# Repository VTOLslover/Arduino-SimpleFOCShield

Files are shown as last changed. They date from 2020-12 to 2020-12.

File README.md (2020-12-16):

# Arduino *Simple**FOC**Shield* *v2.0* - *(testing)*

This is an open-source low-cost Brushless DC (BLDC) motor driver board intended primarily for low-power FOC applications up to 5Amps. The board is fully compatible with the Arduino UNO and all the boards with the standard Arduino headers. The *Simple**FOC**Shield*, in combination with the *Simple**FOC**library* provides user-friendly way to control BLDC motors both in hardware and software.

<p align="">
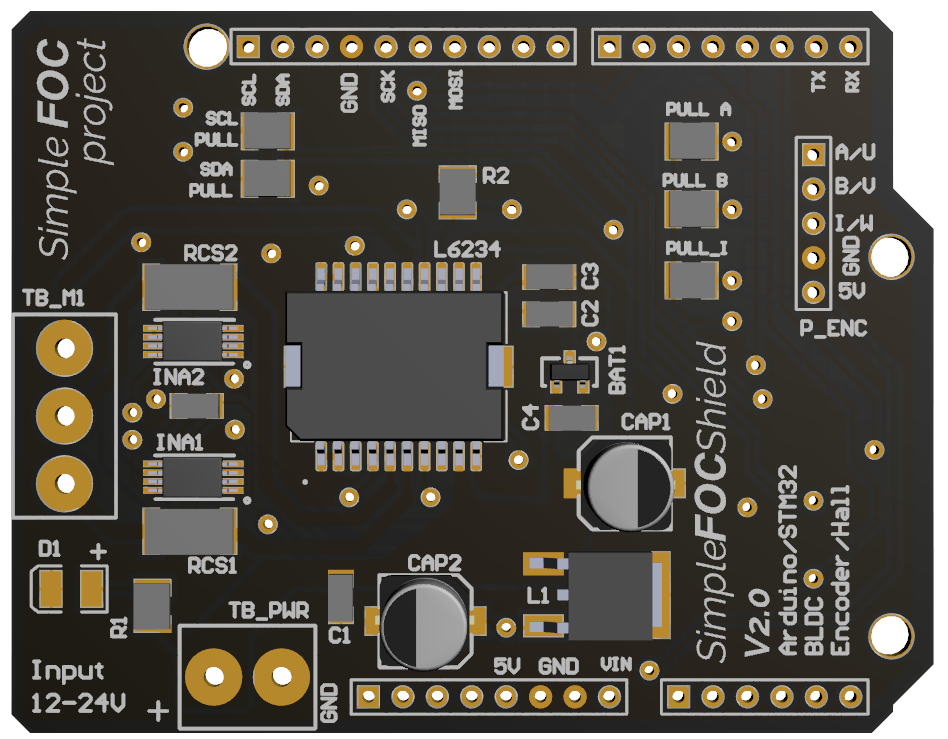
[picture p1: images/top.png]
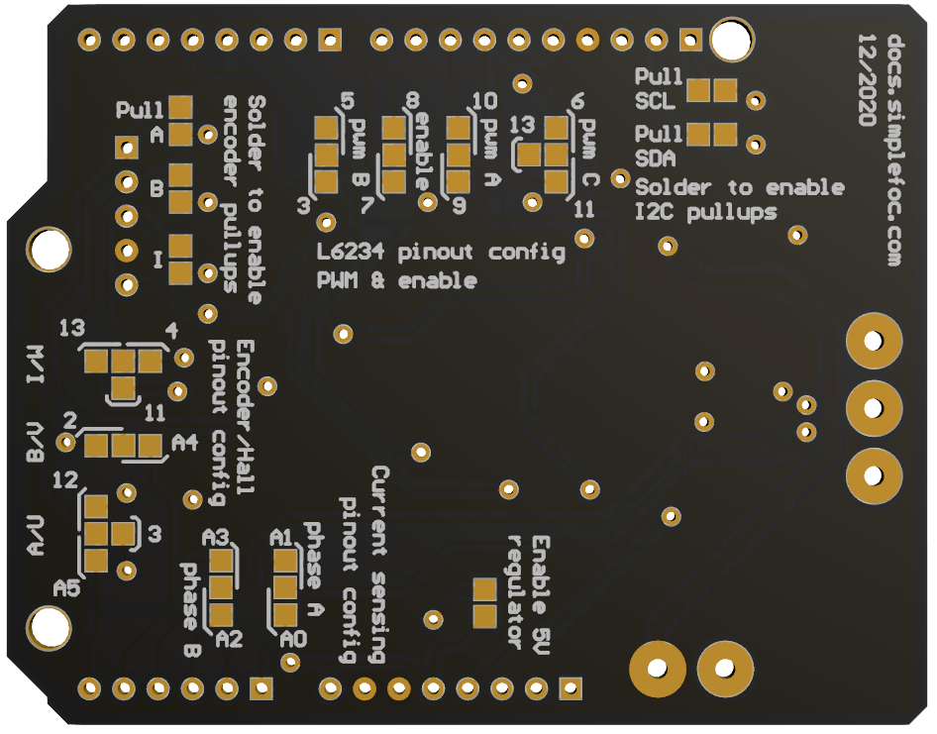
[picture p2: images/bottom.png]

</p>

### Features
- **Plug & play**: In combination with Arduino *Simple**FOC**library* - [github](https://github.com/simplefoc/Arduino-FOC)
- **Low-cost**: Price of €15 - [Check the pricing](https://www.simplefoc.com/simplefoc_shield_product) 
- **Max power 120W** - max current 5A, power-supply 12-24V
   - Designed for Gimbal motors with the internal resistance >10 Ωs. 
- **Stackable**: running 2 motors in the same time
- **Encoder/Hall sensors interface**: Integrated 3.3kΩ pullups (configurable)
- **I2C interface**: Integrated 4.7kΩ pullups (configurable)
- **Configurable pinout**: Hardware configuration - soldering connections
- **Arduino headers**: Arduino UNO, Arduino MEGA, STM32 Nucleo boards...
- **Open Source**: Fully available fabrication files - [how to make it yourself](https://docs.simplefoc.com/arduino_simplefoc_shield_fabrication)

### New Features 
- **In-line Current sensing** 
   - Up to 3Amps bi-directional
   - Real FOC torque control
- 5V voltage regulator
   - configurable - enable/disable
- New pinout for hardware config
- Still optimised for ordering from JLCPCB

### Short YouTube demonstration video :D
<p align="">
<a href="https://youtu.be/G5pbo0C6ujE">

</a>
</p>

## Board versions:

To check the release timeline, click [here](https://github.com/simplefoc/Arduino-SimpleFOCShield/releases) 

Version  |link | Release date | Comment
----- | ----- | ---- | ----
*Simple**FOC**Shield* v1.3 |[release v1.3](https://github.com/simplefoc/Arduino-SimpleFOCShield/releases/tag/v1.3) | 04/20 | Inital release
*Simple**FOC**Shield* v1.3.1 | [release v1.3.1](https://github.com/simplefoc/Arduino-SimpleFOCShield/releases/tag/v1.3.1) | 07/20 | added Nucleo stacking support
*Simple**FOC**Shield* v1.3.2 |[release v1.3.2](https://github.com/simplefoc/Arduino-SimpleFOCShield/releases/tag/v1.3.2) | 09/20 | added I2C pullups
*Simple**FOC**Shield* v1.3.3 |[release v1.3.3](https://github.com/simplefoc/Arduino-SimpleFOCShield/releases/tag/v1.3.3) | 12/20 | addapted L6234 circuit + full Arduino header

## Getting started
You already have your own <span class="simple">Simple<span class="foc">FOC</span>Shield</span>? <br>
[Here is a simple guide how to start preparing your setup](https://docs.simplefoc.com/arduino_simplefoc_shield_getting_started)

## How to get hold of the <span class="simple">Simple<span class="foc">FOC</span>Shield</span> 
- **Fabricate the board yourself**:  Please visit the [board fabrication](https://docs.simplefoc.com/arduino_simplefoc_shield_fabrication) to find out how to manufacture the board yourself!<br>
- **Order the finished and tested board**:  Check out our [shop](https://simplefoc.com/simplefoc_shield_product).

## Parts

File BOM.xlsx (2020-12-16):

Designator | Comment | Manufacturer Part Number or Seeed SKU | Qty | Link
C1 | 1206 100nF | C1206C104M5RECAUTO | 1 | https://www.mouser.com/
C2 | 1206 10nF | C1206C103J3RAUTO | 1 | 'https://www.mouser.com/
C3 | 1206 1uF | C1206X105K3RAC3316 | 1 | 'https://www.mouser.com/
C4 | 1206 220nF | C1206C224J5RECAUTO7210 | 1 | 'https://www.mouser.com/
CAP2 | 10uF | VZH100M1HTR-0606 (https://octopart-clicks.com/click/altium?sku=667-EEH-ZA1E101XP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) | 1 | 'https://www.mouser.com/
CAP1 | 100uF | EEEHAV101XAP (https://octopart-clicks.com/click/altium?sku=667-EEH-ZA1E101XP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) | 1 | 'https://www.mouser.com/
BAT1 | BAT54S | TBAT54S,LM (https://octopart-clicks.com/click/altium?manufacturer=ON%20Semiconductor%20%2F%20Fairchild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) | 1 | 'https://www.mouser.com/
D1 | 1206 red diode | 156120RS75300 | 1 | 'https://www.mouser.com/
L6234 | L6234PD | L6234PD | 1 | 'https://www.mouser.com/
PULL_A, PULL_B, PULL_I | 3.3KOhm 1210 | ERJ-14YJ332U | 3 | 'https://www.mouser.com/
PULL_SDA, PULL_SCL, R2 | 4.7KOhm 1210 | RC1210FR-074K7L | 3 | 'https://www.mouser.com/
R1 | 750Ohm 1210 | ERJ-14NF6200U | 1 | 'https://www.mouser.com/
RCS1, RCS2 | 0.01Ohm 2512 |  | 2
CBY1 | 1206 0.1uF |  | 1
INA1,INA2 | INA240 |  | 2
L1 | L7805 |  | 1
P1, P4 | 8 pin female header long | 920-0086-01 | 1 | 'https://www.mouser.com/
P2 | 10 pin female header long (pack of 6) | 920-0087-01 | 2 | 'https://www.mouser.com/
P3 | 6 pin female header long | 6fx1L-254mm | 2 | 'https://www.mouser.com/
P_ENC | 5pin female/male header | M20-7820546 | 1 | 'https://www.mouser.com/
TB_M1 | terminal connector 3pin 5mm pitch | TB002-500-03BE (https://octopart-clicks.com/click/altium?sku=490-TB002-500-03BE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) | 1 | 'https://www.mouser.com/
TB_PWR | terminal connector 2pin 5mm pitch | TB002-500-02BE (https://octopart-clicks.com/click/altium?sku=490-TB002-500-02BE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) | 1 | 'https://www.mouser.com/

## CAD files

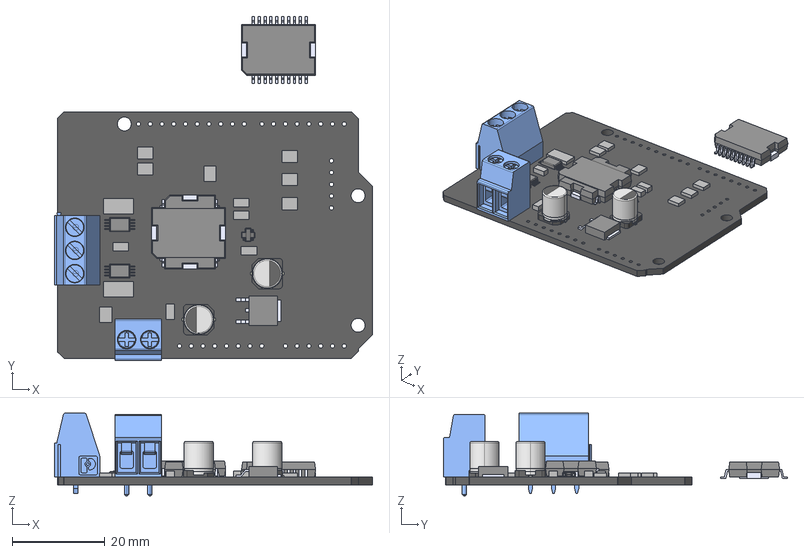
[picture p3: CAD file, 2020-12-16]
3d model/SimpleFOCShield.STEP
68.7 x 74.3 x 17.8 mm
Board
ina240 x 2
User_Library-A3D-003-00012 x 2
l7805
37753_RGB15238730
Extruded x 14
L6234PD x 3
User_Library-BAT54 x 2
2_RGB15238730

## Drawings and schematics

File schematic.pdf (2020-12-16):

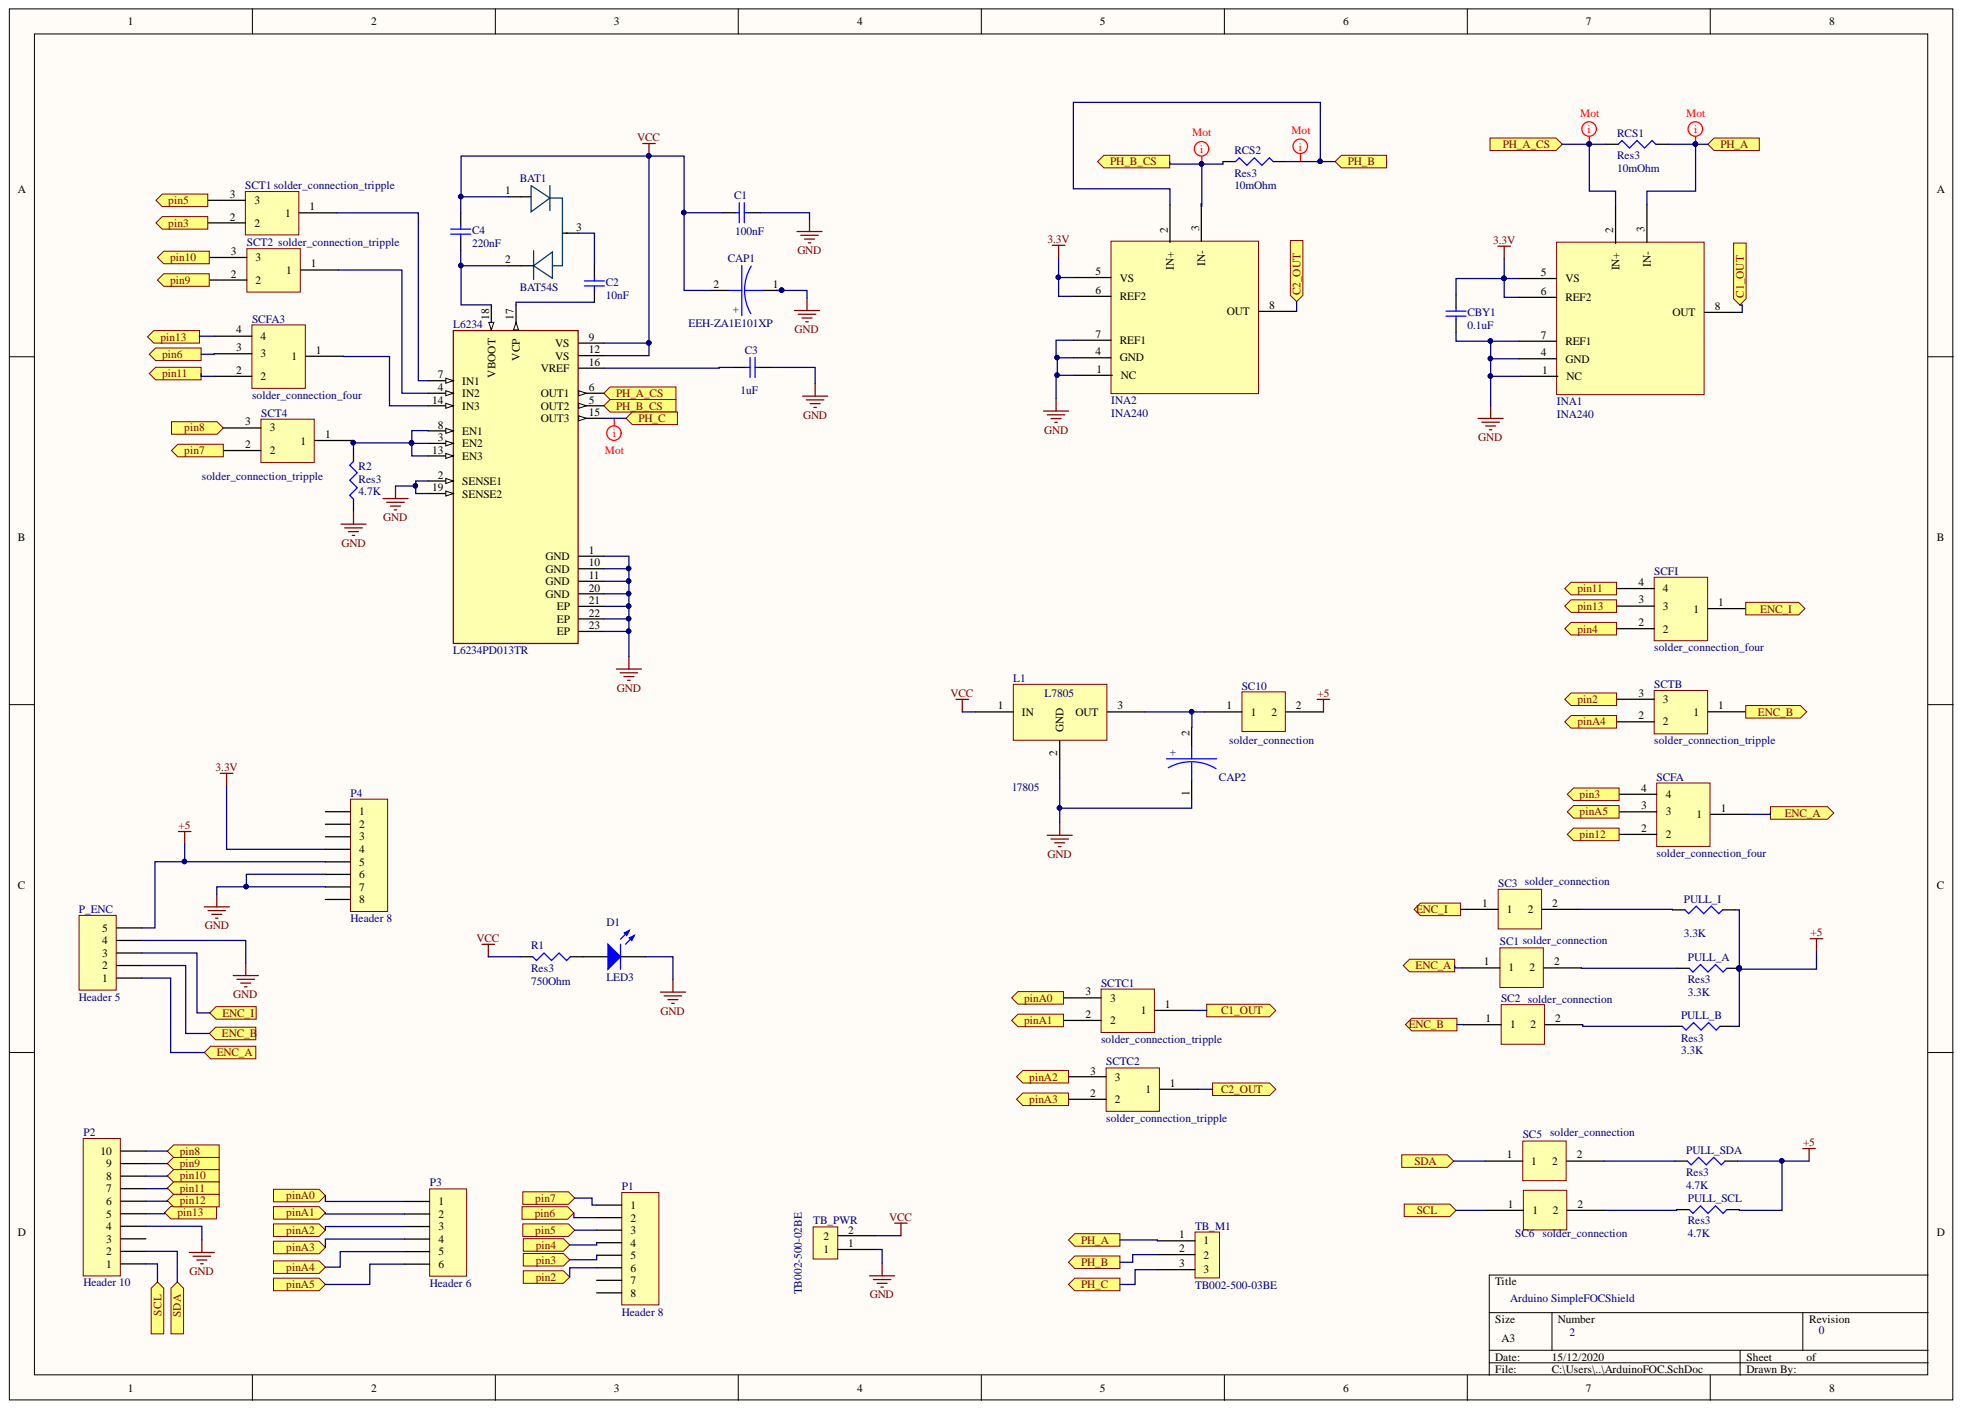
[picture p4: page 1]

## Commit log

2020-11-25 version 2.0
    [ArduinoFOC.GBL, ArduinoFOC.GBO, ArduinoFOC.GBP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]
2020-12-16 version 2.0 update
    [ArduinoFOC.GBL, ArduinoFOC.GBO, ArduinoFOC.GBP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]
